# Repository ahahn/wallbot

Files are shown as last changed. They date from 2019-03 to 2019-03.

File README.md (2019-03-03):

# wallbot
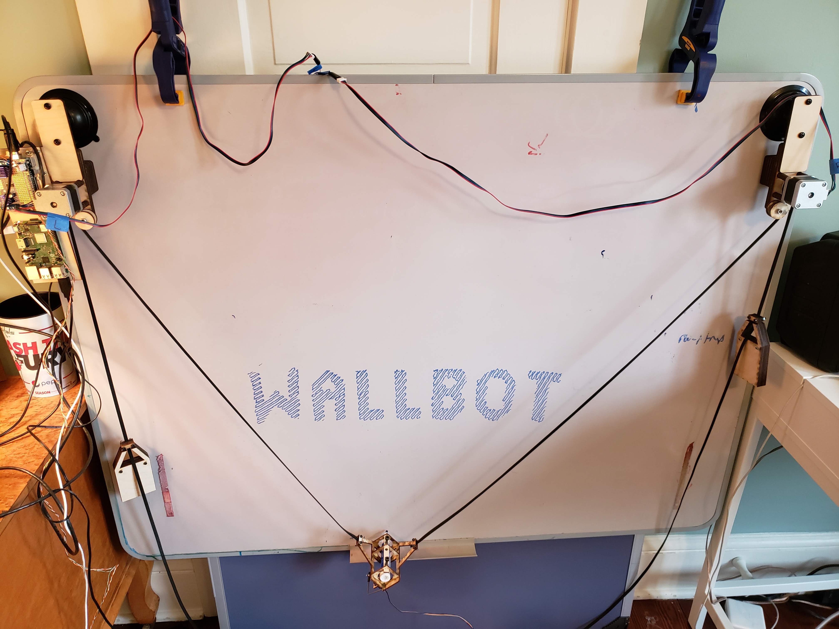
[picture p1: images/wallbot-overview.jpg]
Overview of complete Wallbot Wallbot Overview


This is the complete repo for my wallbot project.
The wallbot is a simple two-motor Cartesian robot that draws on vertical surfaces.  I use it to draw on whiteboards and windows with dry erase markers.

The [designs directory](designs) has all of the laser cut designs to make the physical parts of the machine.
Assembly instructions are included as well.

Other components which are needed for the wallbot:
1) Raspberry pi model 3 (other models will probably work) running raspbian or another linux with node.js installed.
(https://www.amazon.com/Raspberry-Pi-RASPBERRYPI3-MODB-1GB-Model-Motherboard/dp/B01CD5VC92 plus a microSD card > 8GB and a higher amp power cable like this https://www.amazon.com/CanaKit-Raspberry-Supply-Adapter-Listed/dp/B00MARDJZ4 ) (about $55 all together)
2) Arduino UNO (other models will probably work) (about $20)
3) Adafruit motor shield ( https://www.adafruit.com/product/1438 ) (about $20)
4) Heatsinks for motor shield PWM drivers ( https://www.amazon.com/gp/product/B07FDWCR12 ) (about $12)
5) 2 x NEMA-17 Stepper motors (https://www.amazon.com/gp/product/B07C1MVTZC) (about $12)
6) 1 Servo motor
7) 2 x 40 teeth drive belt pulleys w/ 5mm bore (https://www.amazon.com/gp/product/B07K69PFVN) (about $10)
8) 2 x 5m 6mm drive belt (https://www.amazon.com/gp/product/B078SPNKS1) (about $13)
9) 2 Suction cup mounts (like https://www.amazon.com/gp/product/B001447JYG ) (about $25)

That's about $175 of parts all together.

The mounts for the motors, electronics, and pen can all be laser cut from plywood.  The pen mount design should be cut from 1/8" wood, and weights and motor mounts should be cut from 1/4" wood.

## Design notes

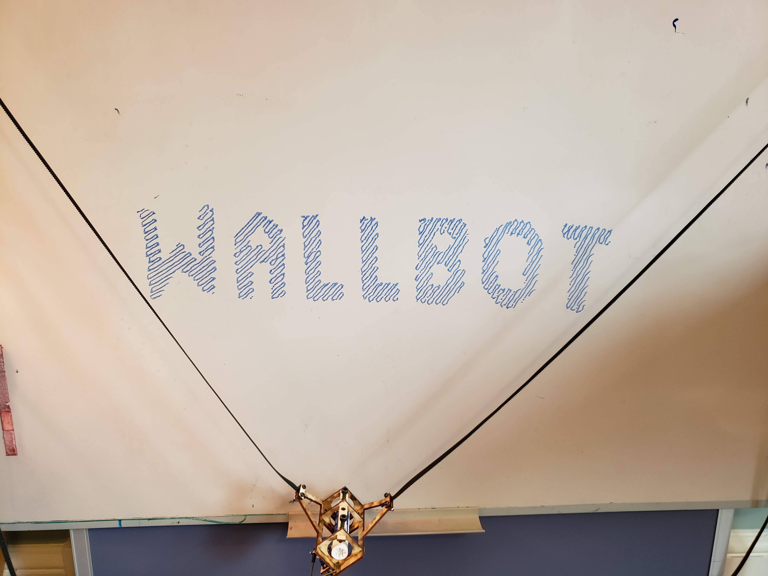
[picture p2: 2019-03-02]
images/wallbot-text.jpg

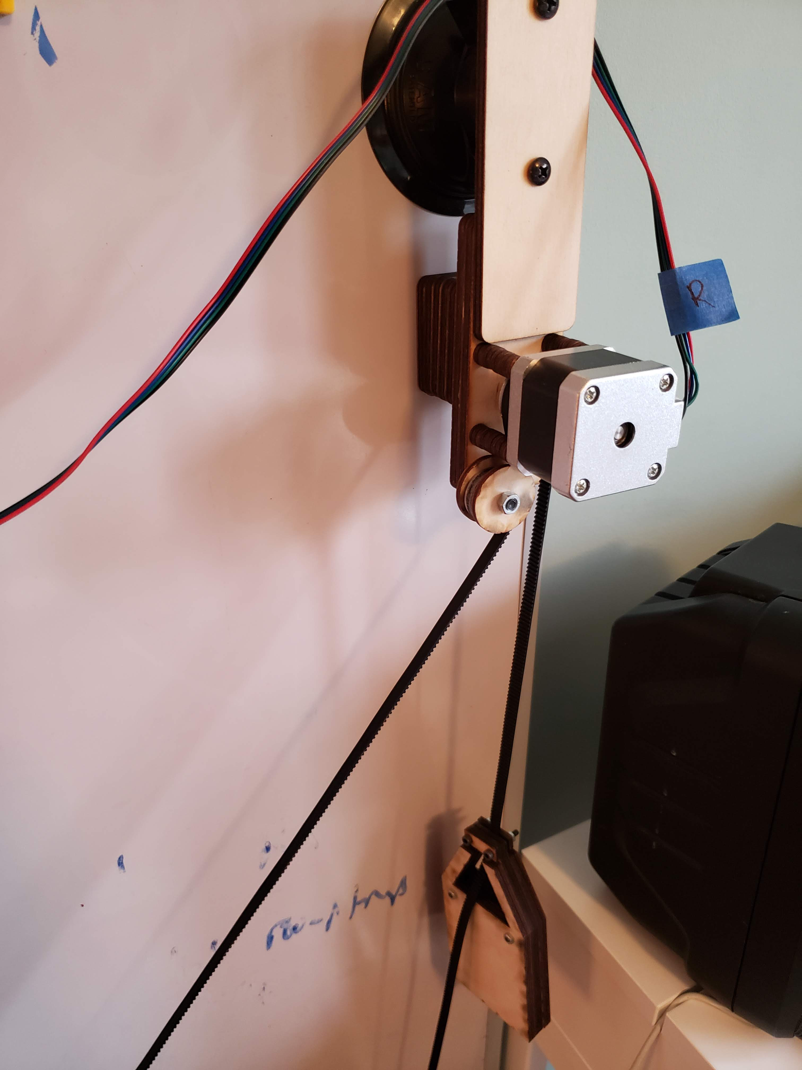
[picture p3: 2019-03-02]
images/right-motor-and-weight.jpg

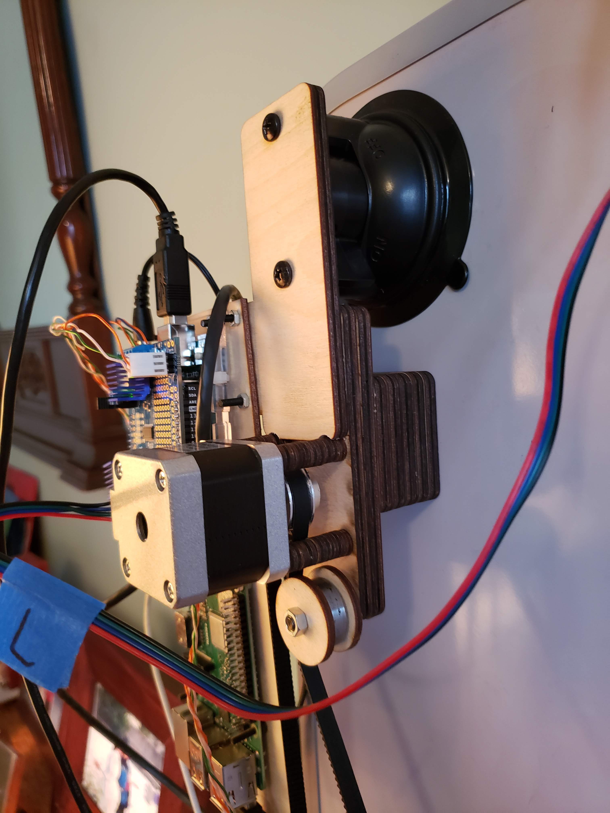
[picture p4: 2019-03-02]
images/left-motor.jpg

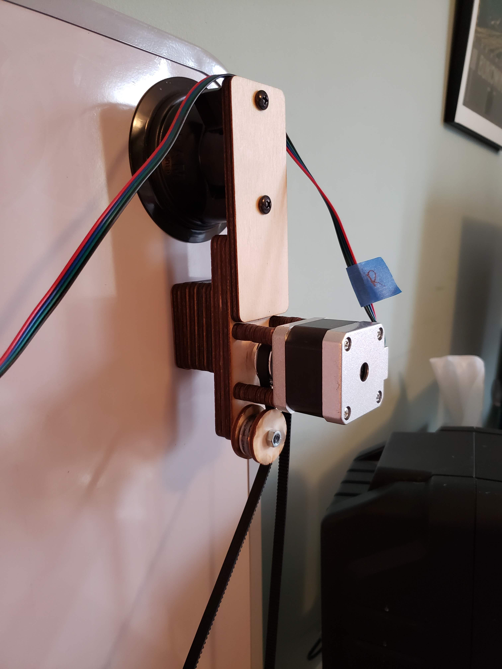
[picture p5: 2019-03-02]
images/right-motor.jpg

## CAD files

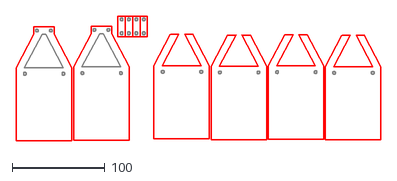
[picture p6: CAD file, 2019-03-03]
designs/weights.dxf
394.1 x 134.7

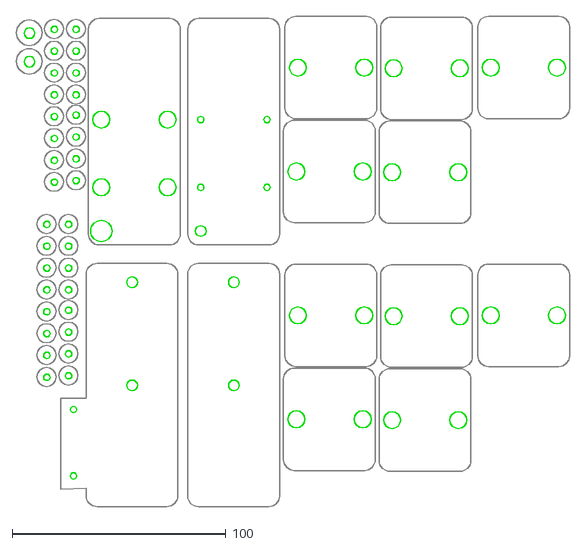
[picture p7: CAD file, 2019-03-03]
designs/motor-mount.dxf
259.1 x 229.7

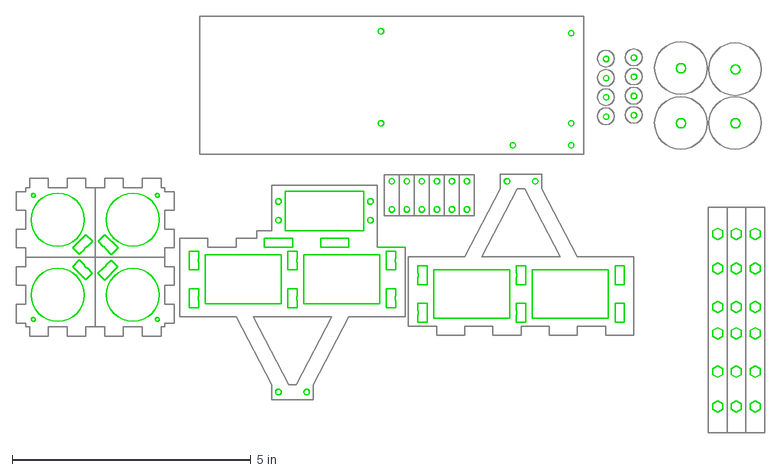
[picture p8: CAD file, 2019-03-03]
designs/pen-holder-single.dxf
15.7 x 8.73 in

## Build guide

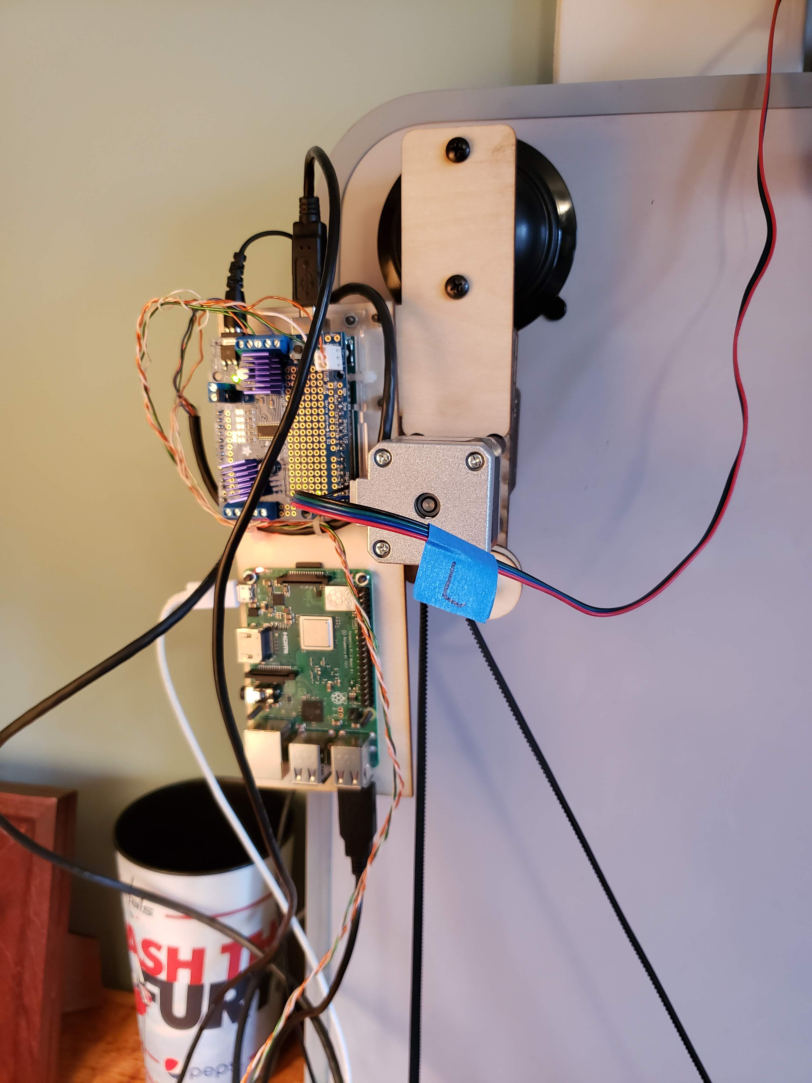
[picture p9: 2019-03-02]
images/left-electronics-assembly.jpg

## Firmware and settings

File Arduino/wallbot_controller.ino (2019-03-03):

#include <Wire.h>
#include <Servo.h> 
#include <Adafruit_MotorShield.h>
//#include <AccelStepper.h>
//#include <MultiStepper.h>

Adafruit_MotorShield AFMS = Adafruit_MotorShield(); 

Adafruit_StepperMotor *myMotor1 = AFMS.getStepper(200, 1);
Adafruit_StepperMotor *myMotor2 = AFMS.getStepper(200, 2);

#define MOTOR_RIGHT 1
#define MOTOR_LEFT 2
#define MOTOR_RIGHT_FORWARD FORWARD
#define MOTOR_RIGHT_BACKWARD BACKWARD
#define MOTOR_LEFT_FORWARD BACKWARD
#define MOTOR_LEFT_BACKWARD FORWARD
// SINGLE DOUBLE INTERLEAVE MICROSTEP
#define STEPPERCOIL SINGLE
#define STEPPERSPEED 2
#define SERVOUP 150
#define SERVODOWN 90
#define USESERVO 1
#ifdef USESERVO
Servo servo1;
int servoAngle = 150;
#endif

//void forwardstep1() {
//  myMotor1->onestep(MOTOR_RIGHT_FORWARD,STEPPERCOIL);
//}
//void backwardstep1() {
//  myMotor1->onestep(MOTOR_RIGHT_BACKWARD,STEPPERCOIL);
//}
//void forwardstep2() {
//  myMotor2->onestep(MOTOR_LEFT_FORWARD,STEPPERCOIL);
//}
//void backwardstep2() {
//  myMotor2->onestep(MOTOR_LEFT_BACKWARD,STEPPERCOIL);
//}
//
//AccelStepper stepper1(forwardstep1, backwardstep1);
//AccelStepper stepper2(forwardstep2, backwardstep2);

// units in mm
//#define canvasWidth 1000
//#define canvasHeight 700
int canvasWidth = 1000;
int canvasHeight = 700;

int curX = canvasWidth / 2;
int curY = canvasHeight / 2;

int stepsRight = 0;
int stepsLeft = 0;

#ifdef DEBUG
int debug = 0;
#endif

void setup() {
  // put your setup code here, to run once:
  Serial.begin(19200);
  Serial.println("in setup");
  AFMS.begin();
  myMotor1->setSpeed(STEPPERSPEED);
  myMotor2->setSpeed(STEPPERSPEED);
  
//  stepper1.setMaxSpeed(100.0);
//  stepper1.setAcceleration(100.0);
//  stepper2.setMaxSpeed(100.0);
//  stepper2.setAcceleration(100.0);
#ifdef USESERVO
  servo1.attach(10);
  servo1.write(servoAngle);
#endif

  Serial.println("ready");
}

void loop() {
  // put your main code here, to run repeatedly:
  if (Serial.available() > 0) {
    delay(5);
    int c = Serial.read();
    if ((c == '?')||(c == 'h')) {
      Serial.print("{\"result\":{\"lines\":[\"ahahn's wallbot v1.0\",");
      Serial.print("\"Available commands:\",");
      Serial.print("\"p - report current position\",");
      Serial.print("\"o - go to origin\",");
      Serial.print("\"f - free stepper motors for manual position adjustment\",");
      Serial.print("\"g <xdist> <ydist> - go distance mm on each axis from current position\",");
      Serial.print("\"c <width> <height> - set width and height of the current canvas\",");
      Serial.print("\"r <steps> - move right motor <steps>\",");
      Serial.print("\"l <steps> - move left motor <steps>\",");
      Serial.print("\"q - servo back- pen down\",");
      Serial.print("\"u - pen up\",");
      Serial.print("\"d - pen down\",");
      Serial.print("\"e - servo forward- pen up\",");
      Serial.print("\"v <level> - verbose messages level\"");
      Serial.println("]}}");
    } else if (c == 'p') {
      Serial.print("{\"result\": {\"positionX\":");
      Serial.print(curX);
      Serial.print(", \"positionY\": ");
      Serial.print(curY);
      Serial.print(",");
      Serial.print("\"stepsRight\":");
      Serial.print(stepsRight);
      Serial.print(", \"stepsLeft\": ");
      Serial.print(stepsLeft);
      Serial.print(", \"servoAngle\": ");
      Serial.print(servoAngle);
      Serial.println("}}");
    } else if (c == 'o') {
      goOrigin();
      Serial.println("{\"result\": {\"message\": \"at origin\"}}");
    } else if (c == 'u') {
      penUp();
      Serial.println("{\"result\": {\"message\": \"pen up\"}}");
    } else if (c == 'd') {
      penDown();
      Serial.println("{\"result\": {\"message\": \"pen down\"}}");
    } else if (c == 'f') {
      myMotor1->release();
      myMotor2->release();
      Serial.println("{\"result\": {\"message\": \"motors freed\"}}");
    } else if (c == 'r') { 
      int steps = Serial.parseInt();
      step(MOTOR_RIGHT,steps);
      Serial.print("{\"result\": {\"message\": \"right move complete\"},");
      Serial.print("\"stepsRight\":");
      Serial.print(stepsRight);
      Serial.print(", \"stepsLeft\": ");
      Serial.print(stepsLeft);
      Serial.println("}");
    } else if (c == 'l') {
      int steps = Serial.parseInt();
      step(MOTOR_LEFT,steps);
      Serial.print("{\"result\": {\"message\": \"left move complete\"},");
      Serial.print("\"stepsRight\":");
      Serial.print(stepsRight);
      Serial.print(", \"stepsLeft\": ");
      Serial.print(stepsLeft);
      Serial.println("}");
    } else if (c == 'c') {
      int wval = Serial.parseInt();
      int hval = Serial.parseInt();
      canvasWidth = wval;
      canvasHeight = hval;
      curX = canvasWidth / 2;
      curY = canvasHeight / 2;
            
      Serial.print("{\"result\": {\"message\":\"done x command\",");
      Serial.print("\"canvasWidth\":");
      Serial.print(canvasWidth);
      Serial.print(", \"canvasHeight\":");
      Serial.print(canvasHeight);
      Serial.print(", \"positionX\":");
      Serial.print(curX);
      Serial.print(", \"positionY\":");
      Serial.print(curY);
      Serial.println("}}");
    } else if (c == 'g') {
      int xval = Serial.parseInt();
      int yval = Serial.parseInt();
      go(xval,yval,0);
      Serial.print("{\"result\": {\"message\":\"done g command\",");
      Serial.print("\"positionX\":");
      Serial.print(curX);
      Serial.print(", \"positionY\":");
      Serial.print(curY);
      Serial.println("}}");
#ifdef USESERVO
    } else if (c == 'q') {
      if (servoAngle > 5) {
        servoAngle = servoAngle - 5;
        servo1.write(servoAngle);
        delay(10);
      }
      Serial.print("{\"result\":{\"message\":\"pen down\",\"distance\":");
      Serial.print(servoAngle);
      Serial.println("}}");
    } else if (c == 'e') {
      if (servoAngle < (180 - 5)) {
        servoAngle = servoAngle + 5;
        servo1.write(servoAngle);
        delay(10);
      }
      Serial.print("{\"result\":{\"message\":\"pen up\",\"distance\":");
      Serial.print(servoAngle);
      Serial.println("}}");
#endif
    }
  }
}

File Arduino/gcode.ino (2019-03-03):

void step(int motor, int steps) {
  #ifdef DEBUG
  if (debug >= 5) {
    Serial.print("stepping motor ");
    Serial.print(motor);
    Serial.print(" ");
    Serial.print(steps);
    Serial.print(" steps");
    Serial.println();
  }
  #endif
  if (motor == MOTOR_RIGHT) {
    stepsRight += steps;
//    if (abs(steps) > 30) {
//      myMotor1->step(5, (steps < 0) ? MOTOR_RIGHT_BACKWARD : MOTOR_RIGHT_FORWARD, STEPPERCOIL);
//      myMotor1->setSpeed(3);
//      myMotor1->step(5, (steps < 0) ? MOTOR_RIGHT_BACKWARD : MOTOR_RIGHT_FORWARD, STEPPERCOIL);
//      myMotor1->setSpeed(4);
//      myMotor1->step(abs(steps)-20, (steps < 0) ? MOTOR_RIGHT_BACKWARD : MOTOR_RIGHT_FORWARD, STEPPERCOIL);
//      myMotor1->setSpeed(3);
//      myMotor1->step(5, (steps < 0) ? MOTOR_RIGHT_BACKWARD : MOTOR_RIGHT_FORWARD, STEPPERCOIL);
//      myMotor1->setSpeed(2);
//      myMotor1->step(5, (steps < 0) ? MOTOR_RIGHT_BACKWARD : MOTOR_RIGHT_FORWARD, STEPPERCOIL);
//    } else {
      myMotor1->step(abs(steps), (steps < 0) ? MOTOR_RIGHT_BACKWARD : MOTOR_RIGHT_FORWARD, STEPPERCOIL);
//    }
  } else {
    stepsLeft += steps;
    myMotor2->step(abs(steps), (steps < 0) ? MOTOR_LEFT_BACKWARD : MOTOR_LEFT_FORWARD, STEPPERCOIL);
  }
}
void goOriginRight() {
  if (stepsRight != 0) {
    #ifdef DEBUG
    if (debug > 0) {
      Serial.print("Right motor stepping ");
      Serial.print((stepsRight < 0)? "FORWARD " : "BACKWARD ");
      Serial.print(abs(stepsRight));
      Serial.println(" steps");
    }
    #endif
    step(MOTOR_RIGHT, stepsRight * -1);
    stepsRight = 0;
  }
}
void goOriginLeft() {
  if (stepsLeft != 0) {
    #ifdef DEBUG
    if (debug > 0) {
      Serial.print("Left motor stepping ");
      Serial.print((stepsLeft < 0)? "FORWARD " : "BACKWARD ");
      Serial.print(abs(stepsLeft));
      Serial.println(" steps");
    }
    #endif
    step(MOTOR_LEFT, stepsLeft * -1);
    stepsLeft = 0;
  }
}
void goOrigin() {
  // lengthen before shortening
  if (stepsLeft > stepsRight) {
    goOriginRight();
    goOriginLeft();
  } else {
    goOriginLeft();
    goOriginRight();
  }
  curX = canvasWidth / 2;
  curY = canvasHeight / 2;
}
long getRightLength(int x, int y) {
  long rxdist = min(canvasWidth,canvasWidth - x);
  long ydist = max(0,min(y,canvasHeight));
  #ifdef DEBUG
  if (debug >= 3) {
    Serial.print("rxdist ");
    Serial.println(rxdist);
    Serial.print("ydist ");
    Serial.println(ydist);
  }
  #endif
  long rs = rxdist *rxdist;
  long ys = ydist*ydist;
  #ifdef DEBUG
  if (debug >= 3) {
    Serial.print("right squared ");
    Serial.println(rs);
    Serial.print("y squared ");
    Serial.println(ys);
  }
  #endif
  long rtot = rs + ys;
  double rl = sqrt(rtot);
  #ifdef DEBUG
  if (debug >= 3) {
    Serial.print("rl is ");
    Serial.println(rl);
  }
  #endif
  return (long(sqrt(rs+ys)));
}
long getLeftLength(int x, int y) {
  long lxdist = max(0,x);
  long ydist = max(0,min(y,canvasHeight));
  #ifdef DEBUG
  if (debug >= 3) {
    Serial.print("lxdist ");
    Serial.println(lxdist);
    Serial.print("ydist ");
    Serial.println(ydist);
  }
  #endif
  long ls = lxdist * lxdist;
  long ys = ydist*ydist;
  #ifdef DEBUG
  if (debug >= 3) {
    Serial.print("left squared ");
    Serial.println(ls);
    Serial.print("y squared ");
    Serial.println(ys);
  }
  #endif
  double ll = sqrt(ls+ys);
  #ifdef DEBUG
  if (debug >= 3) {
    Serial.print("ll is ");
    Serial.println(ll);
  }
  #endif
  return(long(sqrt(ls+ys)));
}
void go(int x, int y) {
  go(x, y, 0);
}
void go(int x, int y, int byArcs) {
  #ifdef DEBUG
  if (debug >= 1) {
    Serial.print("go distance ");
    Serial.print(x);
    Serial.print(" ");
    Serial.print(y);
    Serial.println();
    Serial.print("to position ");
    Serial.print(curX + x);
    Serial.print(" ");
    Serial.print(curY + y);
    Serial.println();
  }
  #endif
  long rightLen = getRightLength(curX + x, curY + y);
  long leftLen = getLeftLength(curX + x, curY + y);
  long curRightLen = getRightLength(curX, curY);
  long curLeftLen = getLeftLength(curX, curY);
  #ifdef DEBUG
  if (debug >= 1) {
    Serial.print("current right len ");
    Serial.println(curRightLen);
    Serial.print("current left len ");
    Serial.println(curLeftLen);
    Serial.print("target right len ");
    Serial.println(rightLen);
    Serial.print("target left len ");
    Serial.println(leftLen);
  }
  #endif
  // go there!
  int dr = (rightLen - curRightLen) * 2;
  int dl = (leftLen - curLeftLen) * 2;
  #ifdef DEBUG
  if (debug >= 1) {
    Serial.print("dr " );
    Serial.println(dr);
    Serial.print("dl " );
    Serial.println(dl);
  }
  #endif
  if (byArcs != 0) {
    step(MOTOR_RIGHT, dr);
    step(MOTOR_LEFT, dl);
  } else {
    int numSteps = max(abs(dr),abs(dl));
    #ifdef DEBUG
    if (debug >= 1) {
      Serial.print("steps is ");
      Serial.println(numSteps);
    }
    #endif
    int rSteps = 0;
    int lSteps = 0;
    double rsUnit = double(dr)/numSteps;
    double lsUnit = double(dl)/numSteps;
    #ifdef DEBUG
    if (debug >= 1) {
      Serial.print("rsUnit ");
      Serial.print(rsUnit);
      Serial.print(" lsUnit ");
      Serial.println(lsUnit);
    }
    #endif
    for (int i = 0; i < numSteps;i++) {
      int thisRS = rsUnit * (i + 1);
      int thisLS = lsUnit * (i + 1);
      if (thisRS != rSteps) {
        #ifdef DEBUG
        if (debug >= 3) {
          Serial.print("thisRS is ");
          Serial.print(thisRS);
          Serial.print(" rSteps ");
          Serial.print(rSteps);
          Serial.print(" moving ");
          Serial.println(thisRS - rSteps);
        }
        #endif
        step(MOTOR_RIGHT,thisRS - rSteps);
        rSteps = thisRS;
      }
      if (thisLS != lSteps) {
            #ifdef DEBUG
        if (debug >= 3) {
          Serial.print("thisLS is ");
          Serial.print(thisLS);
          Serial.print(" lSteps ");
          Serial.print(lSteps);
          Serial.print(" moving ");
          Serial.println(thisLS - lSteps);
        }
        #endif
        step(MOTOR_LEFT,thisLS - lSteps);
        lSteps = thisLS;
      }
    }
    if (rSteps != dr) {
          #ifdef DEBUG
      if (debug >= 1) {
        Serial.print("finishing right with ");
        Serial.print(dr - rSteps);
        Serial.println(" steps");
      }
      #endif
      step(MOTOR_RIGHT,dr - rSteps);
    }
    if (lSteps != dl) {
                #ifdef DEBUG
      if (debug >= 1) {
        Serial.print("finishing left with ");
        Serial.print(dl - lSteps);
        Serial.println(" steps");
      }
      #endif
      step(MOTOR_LEFT,dl - lSteps);
    }
  }

  curX = curX + x;
  curY = curY + y;
}
void penUp() {
  while (servoAngle < SERVOUP) {
    servoAngle = servoAngle + 5;
    servo1.write(servoAngle);
    delay(20);
  }
}
void penDown() {
  delay(60);
  while (servoAngle > SERVODOWN) {
    servoAngle = servoAngle - 5;
    servo1.write(servoAngle);
    delay(15);
  }
}

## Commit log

2019-01-31 adding arduino code
2019-01-31 fixing origin on arduino, changing H line drawing
    [gcode.ino, wallbot-command.js]
2019-01-31 fixing slicing bottom corner; adding test and debug modes for logging
    [wallbot-command.js]
2019-02-01 restructured letter definitions; fixed html display of drawings
    [wallbot-command.js]
2019-02-02 fixing loop end error
    [wallbot-command.js]
2019-02-06 fixing slicing of i
    [wallbot-command.js]
2019-02-08 finishing upper case alphabet; widening canvas; trying to fix block alignment issues
    [wallbot-command.js]
2019-02-08 fixing error on all missing letters
    [wallbot-command.js]
2019-02-09 adding smothing to letters; fixing spacing between block letters
    [wallbot-command.js]
2019-02-09 fixing inter-letter move for uni; removing leftover commands when writing
    [wallbot-command.js]
2019-02-09 fixing letter corruption with scale 1; starting to add newlines
    [wallbot-command.js]
2019-02-10 narrowing and smoothing letters; fixing null parameter actions
    [wallbot-command.js]
2019-02-10 current arduino code
2019-02-10 report liftgap with status; fix one infinite loop in adjustments
    [wallbot-command.js]
2019-02-10 backing out slicing change; fixing newline
    [wallbot-command.js]
2019-02-14 reverting canvas command after arduino reupload
    [wallbot-command.js]
2019-03-02 trying to fix newline x spacing after multi-char write
    [wallbot-command.js]
2019-03-02 trying to fix newline x spacing after multi-char write again
    [wallbot-command.js]
2019-03-02 trying again to fix newline issue
    [wallbot-command.js]
2019-03-03 fixing bug in canvas command; make origin command lengthen shorter side first
    [gcode.ino, wallbot_controller.ino]
2019-03-03 adding dxf version of designs
    [motor-mount.dxf, pen-holder-single.dxf, weights.dxf]
2019-03-04 backing out recurion fix
    [wallbot-command.js]
